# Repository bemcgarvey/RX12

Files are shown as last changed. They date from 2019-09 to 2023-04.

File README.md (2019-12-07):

# RX12  
## A 12 channel radio control receiver that uses one to three Spektrum compatible satellite receivers.

### Features:  
* Up to 12 channels
* One to three satellite receivers for full diversity
* Works with DSMX or DSM2 satellites
* 22ms or 11ms output rate  
* Optional PPM output (up to 8 channels) or S.Bus output (12 channels)
* Preset or hold failsafe modes
* PC client program with serial connection
* Simple data logging of multiple flights
* 32 bit microcontroller at 120MHz

Note: This is not a Spektrum DSMX or DSM2 product, nor is it a copy of a Spektrum DSM2 or DSMX product. The Spektrum, DSMX and DSM2 brand is a trademark of Horizon Hobby, Inc.

User manual is [here](https://github.com/bemcgarvey/RX12/blob/master/docs/RX12%20Manual.pdf)  
Gerber files and schematics can be found in PCB and Schematic folders.  
Firmware built with XC32 2.10 and MPLAB X.  Client code built with Qt 5.12  

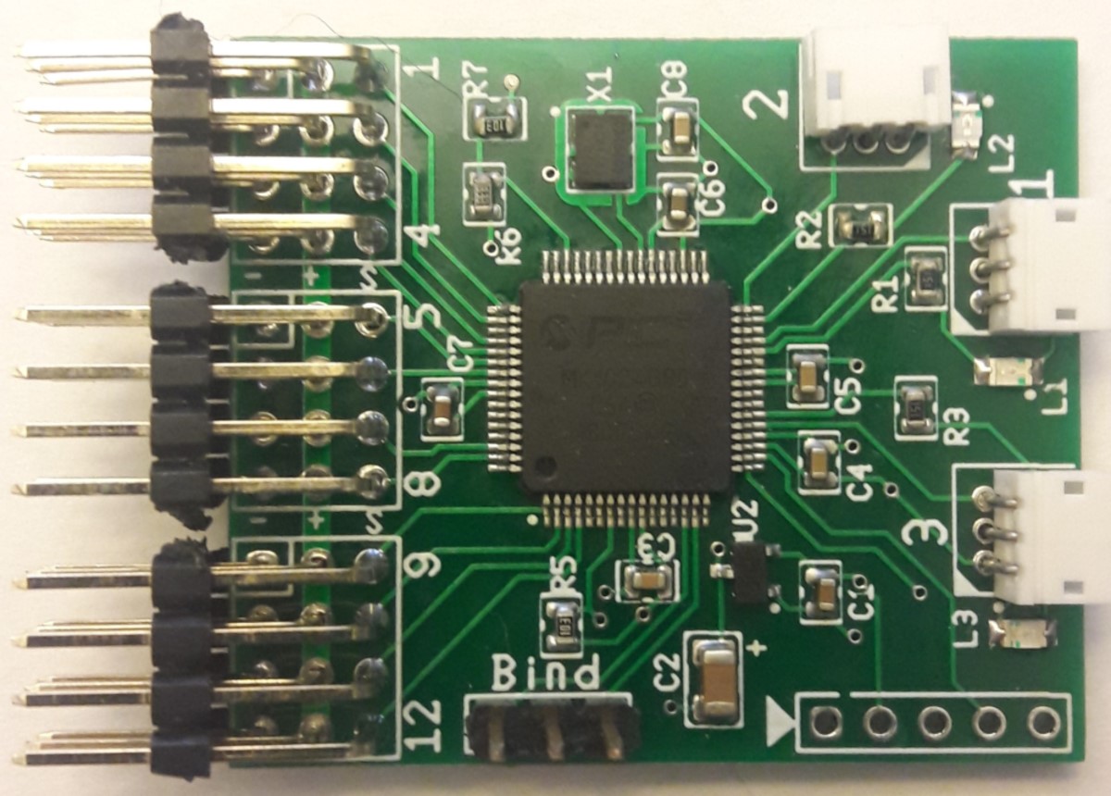
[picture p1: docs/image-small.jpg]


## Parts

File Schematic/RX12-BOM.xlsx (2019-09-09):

Quantity | Description | RefDes | Package | Digikey Part
3 | ZH-3 Side connectors | J4, J5, J6 | Ultiboard\ZH-3-Side | 455-1670-ND
3 | Headers, HDR3X4 | J2, J3, J8 | Ultiboard\HDR3X4
1 | VoltageRegulator, AP2210N-3.3 | U2 | Philips\SOT-23 | AP2210N-3.3TRG1DICT-ND (https://www.digikey.com/product-detail/en/diodes-incorporated/AP2210N-3.3TRG1/AP2210N-3.3TRG1DICT-ND/4505294)
1 | CAPACITOR, 2.2µF | C1 | Ultiboard\C0603
1 | CAPACITOR, 10µF | C2 | Ultiboard\C1206
1 | HEADERS_TEST, HDR1X5 | J1 | Generic\HDR1X5
1 | PIC32, PIC32MKxxxGPD/E064 | U1 | Microchip\TQFP-64(PT)
1 | Xtal, Osc 24 MHz | X1 | Osc-3225 | DSC6001CI2A-024.0000-ND (https://www.digikey.com/product-detail/en/microchip-technology/DSC6001CI2A-024.0000/DSC6001CI2A-024.0000-ND/7732678)
3 | LED_green | L1, L2, L3 | Ultiboard\0805LED
3 | RESISTOR, 150Ω | R1, R2, R3 | Ultiboard\R0603
6 | CAPACITOR, 0.1µF | C3, C4, C5, C6, C7,C8 | Ultiboard\C0603
2 | RESISTOR, 10kΩ | R5, R7 | Ultiboard\R0603
1 | RESISTOR, 33kΩ | R6 | Ultiboard\R0603
1 | HEADERS_TEST, HDR1X3 | J7 | Generic\HDR1X3

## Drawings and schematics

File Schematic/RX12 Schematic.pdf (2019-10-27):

0

1

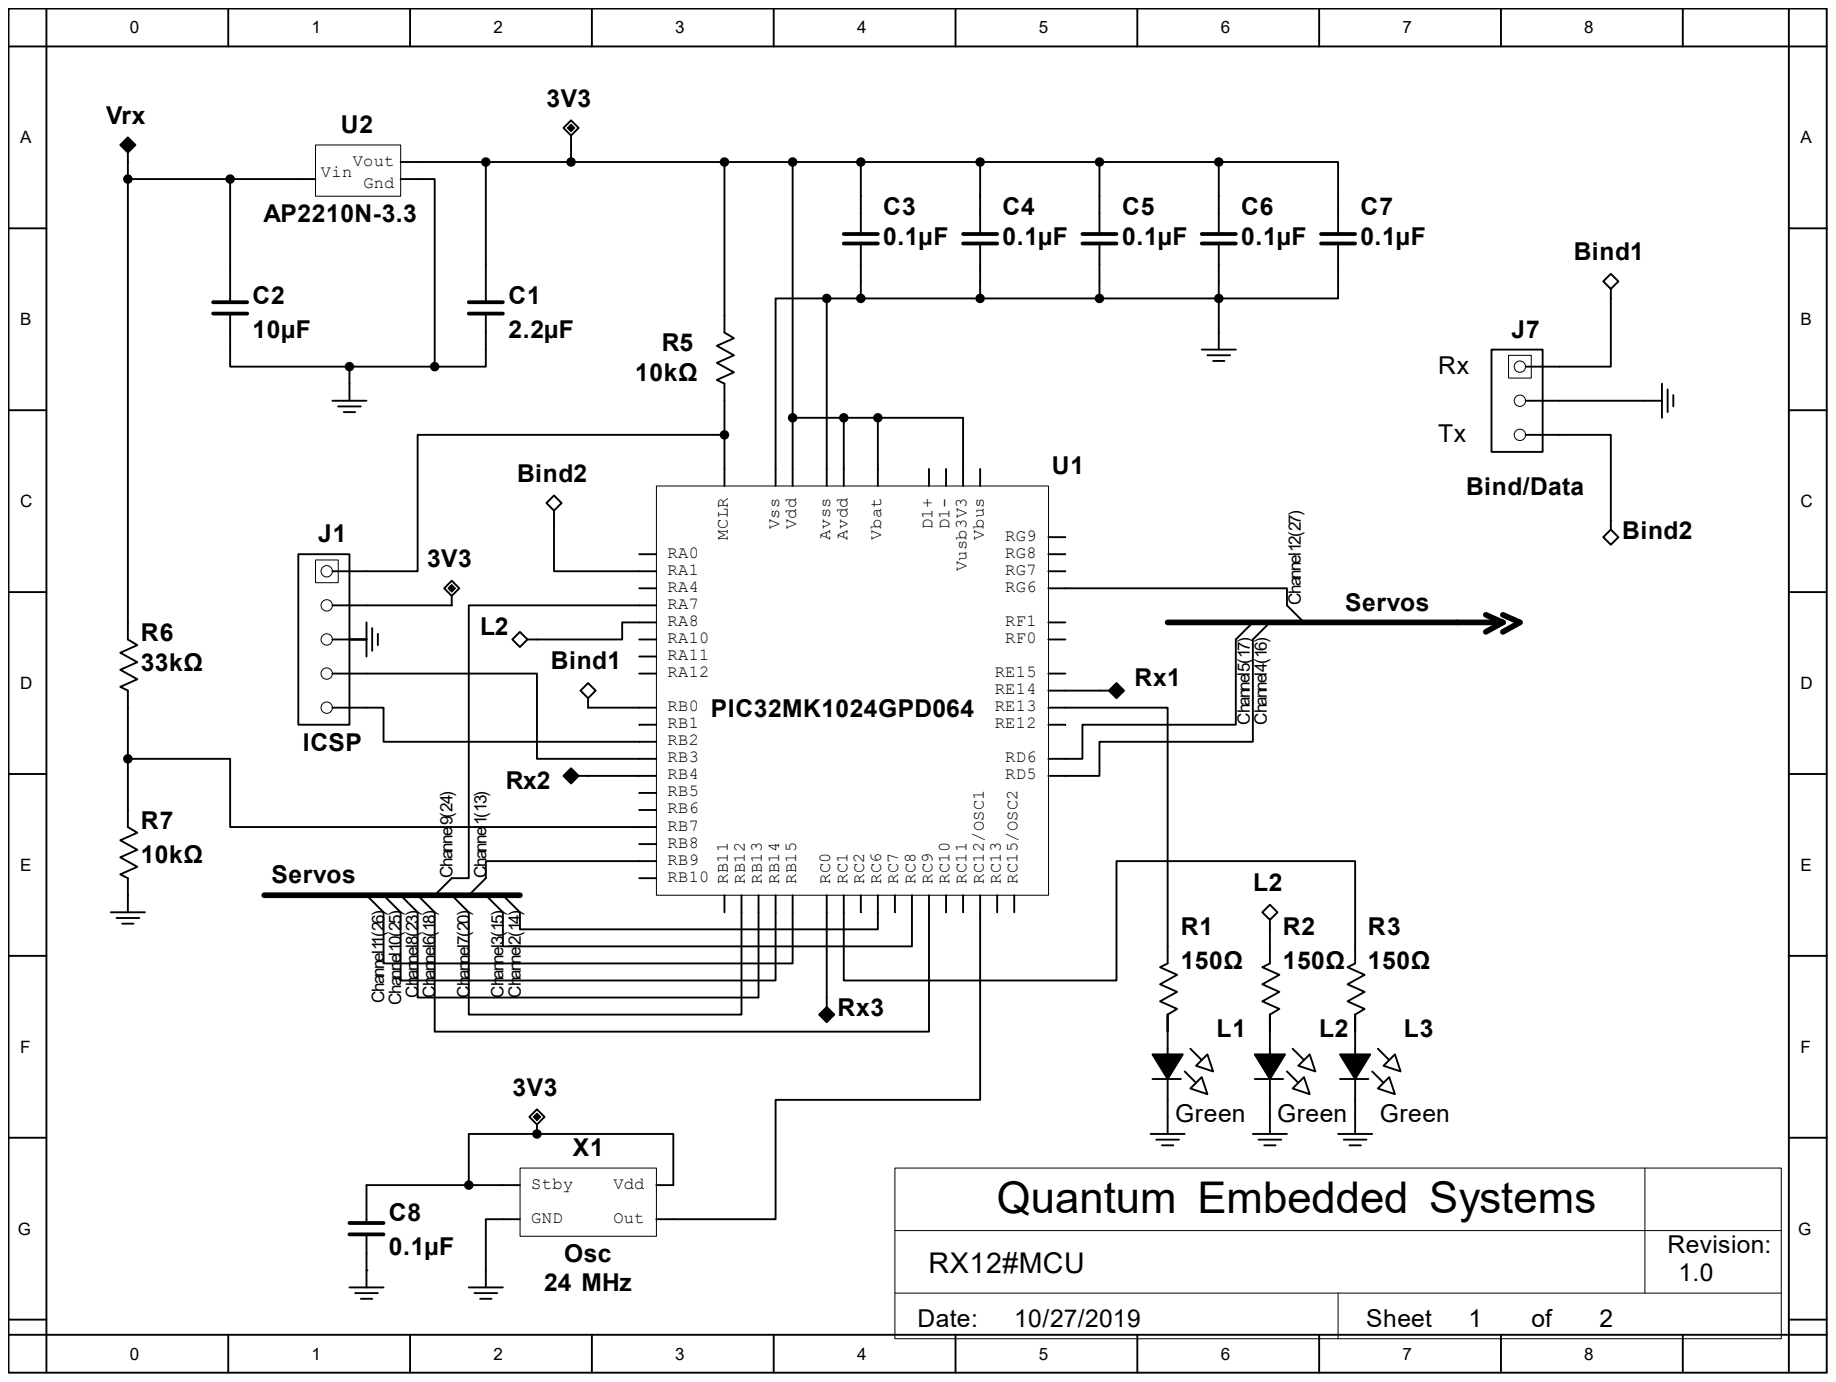
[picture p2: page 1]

0

1

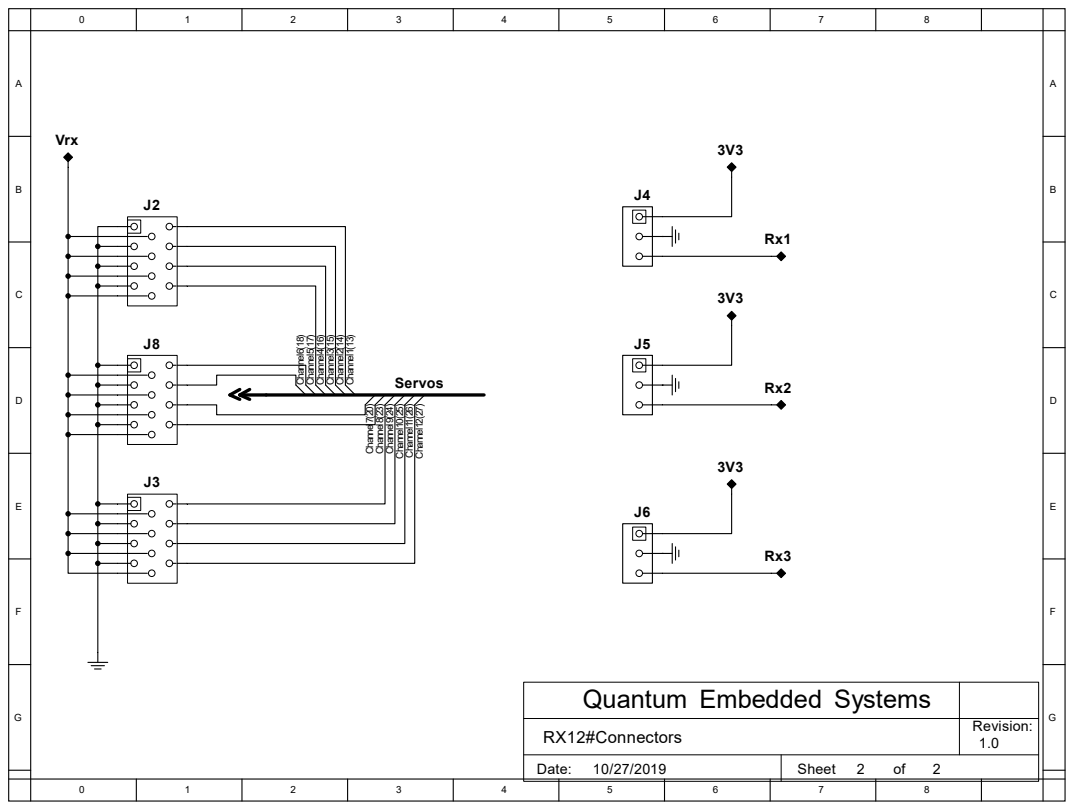
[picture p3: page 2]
Vrx; Channel4⁽ 16⁾ Channel3⁽ 15⁾ Channel2⁽ 14⁾ Channel1⁽ 13⁾; Servos; Channel6⁽ 18⁾ Channel5⁽ 17⁾; Channel7⁽ 20⁾ Channel8⁽ 23⁾ Channel9⁽ 24⁾ Channel10⁽ 25⁾ Channel11⁽ 26⁾ Channel12⁽ 27⁾; Date:; Sheet; Revision:; RX12#Connectors

Quantum Embedded Systems

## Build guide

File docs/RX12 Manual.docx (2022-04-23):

RX12

Manual

Version 1.5

April 2022

Firmware Version 1.8

Software Version 1.4

# Table of Contents

1. Overview
2. Connections and LED codes
3. Binding
4. Output formats and channel order
5. Client software
6. Data logging

# Overview

The RX12 receiver turns one or more DSMX/DSM2 satellite receivers into a full capability receiver with up to 12 channels. It supports the following features:

- Supports DSMX-11ms, DSMX-22ms, DSM2-2048 and DSM2-1024 transmitter modes. Note that you must use DSMX-22ms to receive 12 channels. The maximum channels in DSMX-11ms mode is 10. This is a Spektrum limitation and not an issue with the receiver.
- 12 channel PWM or S.Bus output with 22ms or 11ms servo frame rate or a single PPM output with up to 8 channels. The S.Bus outputs include all 18 S.Bus channels but only channels 1-10 are output on the PWM pins.
- Configurable failsafe - hold (no throttle signal) or user preset failsafe
- Can support up to three satellite receivers for full diversity.
- Limited data logging.
- Updatable firmware.

Note: This is not a Spektrum DSMX or DSM2 product, nor is it a copy of a Spektrum DSM2 or DSMX product. The Spektrum, DSMX and DSM2 brand is a trademark of Horizon Hobby, Inc.

# Connections and LED codes

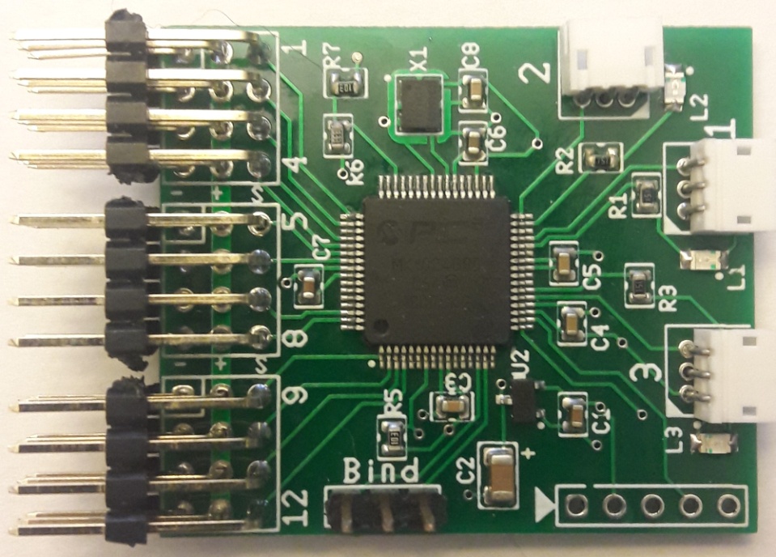
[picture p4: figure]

Tx Gnd Rx

Satellite Ports

L1, L2 and L3 are LED1, LED2 and LED3

ICSP Port

Bind/Serial Port

Servo outputs

Connection descriptions

Satellite ports: Connect one or more DSMX/DSM2 satellites to these ports. Any port may be used, they do not need to be connected in any order. You can connect satellites to any combination of ports. The only requirement is that all satellites must be of the same type, either all DSMX or all DSM2. Each port has an associated LED for status indication.

Bind/Serial port: Used to bind the receiver to the transmitter and for serial communication to a PC. See the Binding section of the manual for information on binding. See the Client Software section for information on serial communication.

ICSP port: Used to update the firmware. Not normally used.

Servo outputs: Connections to the servos. The channels are labeled on the board. Channels 1 – 4 are grouped together then 5 – 8 and 9 – 12. Channels 11 and 12 can also be used during the binding process. See the Binding section for details. Channel 12 is used for PPM output if enabled. Channels 11 and 12 are used for S.Bus outputs if enabled. The signal pin is the upper pin (or rightmost if oriented as in the picture above on top pin versions). The ground pin is the bottom (or leftmost) pin. The center pin is power.

Led codes

LED1 On solid = satellite connected and receiving data

Four flashes at startup = Logging enabled

LED2 On solid = satellite connected and receiving data

Two flashes at startup = Preset failsafe mode

LED3 On solid = satellite connected and receiving data or serial connection established

No flash at startup = PWM with 22ms servo frame

One flash at startup = PWM with 11ms servo frame

Two flashes at startup = PPM mode

Three flashes at startup = S.Bus mode with 22ms servo frame

Four flashes at startup = S.Bus mode with 11ms servo frame

10 flashes at startup = bind mode

# Binding

To bind the receiver to a transmitter follow the steps below.

1. Connect one or more satellite receivers to the satellite ports.
2. Place a bind plug on the bind connector.
3. If you are using DSM2 satellites place a bind plug on Channel 11.
4. If you want to enable 11ms output frame rate place a bind plug on Channel 12. This can also be enabled at a later time either with a bind process or with the PC software.
5. Connect the receiver to an ESC or battery. LED3 should blink rapidly 10 times and the satellites should blink to indicate bind mode.
6. Place the transmitter into bind mode and complete the bind. DO NOT unplug the bind plug at this time unless you want to enable preset failsafe (see next step.)
7. To enable the preset failsafe do the following. Go to step 8 for normal failsafe.
  a. Use the transmitter to set the servos in the desired positions.
  b. With the servos in the correct positions remove the bind plug.
  c. You can now power off the receiver.
8. For normal failsafe (no signal to throttle, all other channels hold) remove the power from the receiver BEFORE removing the bind plug. Don’t forget to remove the bind plug!

Note: Some servos may be detected as a bind plug. When binding it is best not to have a servo plugged into channels 11 or 12 as it may be detected as a bind plug. If you must have a servo plugged into these channels plug it in after LED3 stops flashing.

To enable/disable 11ms output frame rate after the receiver has been bound:

1. Plug a bind plug into the bind port.
2. Plug a bind plug into Channel 12 to enable 11 ms mode. Leave Channel 12 open to disable 11ms mode.
3. Power the receiver. LED3 will blink 10 times and the satellites will be in bind mode.
4. DO NOT rebind the transmitter. After the receiver quits blinking remove the power THEN remove the bind plugs. The next time the receiver is powered up it will blink LED3 to indicate it is in 11ms mode.

Note that 11ms output frame rate is independent from the transmitter frame rate. You may use 11ms output with DSMX-22ms mode or use 22ms output with DSMX-11ms mode. Any combination is allowed. However, you should only use the 11ms output with digital servos.

# Output formats and channel order

The receiver can output to the servos or a flight controller in the following formats:

- Standard PWM outputs on the 12 numbered servo output pins.
- PPM output of up to 8 channels on the Channel 12 pins. In PPM mode there is no output on the channel 1 – 11 pins.
- S.Bus output of up to 18 channels on Channel 11 and 12 pins. Channels 1 – 10 are also output on the PWM pins at 11ms or 22ms as selected during bind or by the client software.

To switch to PPM or S.Bus output you must use the client software to switch modes. See the next section for details on the client software.

Channel ordering

For PWM output the channels follow the standard Spektrum order:

2. Throttle
3. Aileron
4. Elevator
5. Rudder
6. Gear
7. Flaps
8. Aux1
9. Aux2
10. Aux3
11. Aux4
12. Aux5
13. Aux6

S.Bus and PPM outputs use the Futaba AETR ordering:

(Note: The order below is the channel order for the S.Bus outputs. The PWM pins will output with the order shown above for PWM outputs.)

(Note: PPM only supports channels 1-8)

1. Aileron
2. Elevator
3. Throttle
4. Rudder
5. Gear
6. Flaps
7. Aux1
8. Aux2
9. Aux3
10. Aux4
11. Aux5
12. Aux6

# Client Software

The receiver can be connected to a PC through the bind/serial port. The client software can be used to read or set some of the configuration settings. It can also be used to retrieve data logged during previous flights. To connect the receiver to a PC you will need a USB to Serial bridge that supports 3.3V levels.

To connect:

1. Make sure the USB to Serial adapter is set for 3.3V. A 5V adapter will damage or destroy the receiver.
2. Connect the ground of the adapter to the middle pin of the bind port.
3. Connect the TX of the adapter to the RX pin of the bind port (see picture in Connections section.)
4. Connect the RX of the adapter to the TX pin of the bind port.
5. Plug the USB to Serial adapter into your computer.
6. Connect an ESC or battery to the receiver. LED3 should light up and remain on.
7. Start the client software.
8. Select the Port menu then select the port that corresponds to your USB to Serial adapter. The status bar at the bottom of the window should show that you are connected.
9. Click the Read button to read the settings.
10. Make any changes you want and then click the Save button to save them to the receiver.
11. To download flight logs change to the Data tab. Select the number of logs to download (starting with the most recent) and click the Load button.
12. Clicking the Reset Log button will clear all current logs and restart the numbering at 1.

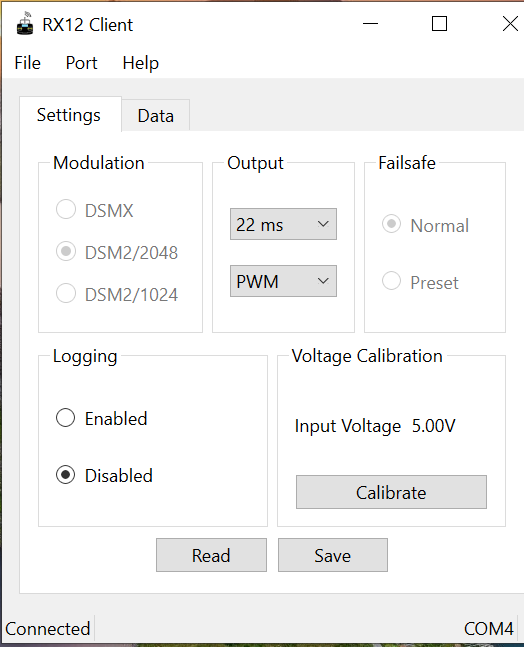
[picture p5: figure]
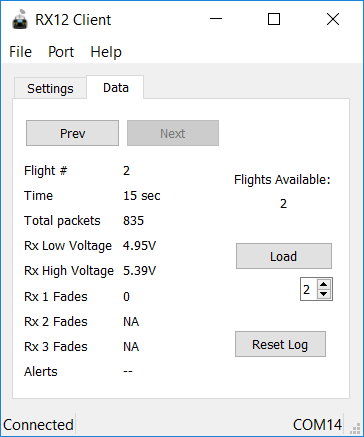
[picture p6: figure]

Voltage Calibration

The voltage input must be calibrated before it will give meaningful results. You can do a one point or two point calibration. A two point calibration is more accurate but requires two different voltages with at least 1.0V difference. A 2.0V or more difference is recommended. This will require a variable power supply that can be connected to the receiver

To perform a one point calibration:

1. With the receiver connected to the serial adapter and powered on, accurately measure the input voltage to the receiver.
2. Click the calibrate button.
3. Enter the measured input voltage in the dialog.
4. Click Next
5. Click Single Value to complete the calibration.

To perform a two point calibration

1. While connected to the serial adapter and powered on set the input voltage to the receiver to a known value between 4.0V and 12.0V.
2. Click the calibrate button.
3. Enter the input voltage in the dialog.
4. Click Next
5. Set the input voltage to a new value. It can be higher or lower than the first voltage but should be at least a one volt difference. It is best to use voltages that cover the expected operating range of the receiver.
6. Enter the new input voltage in the dialog.
7. Click Next to complete the calibration.

# Data Logging

If enabled the receiver will log the following data for each time it is powered on:

- Power on duration
- Total packets received by all satellites
- Input high and low voltage.
- Fades for each satellite.
- Any error conditions detected including activation of the failsafe feature.

Notes:

- Data is sampled continuously but is only saved to flash memory every second.
- In the event of a power failure or brownout the last second of data may be lost.
- Voltages are checked every millisecond.
- Fades are recorded with each satellite packet.
- It is not recommended to use data logging for every flight. Continuous use will eventually wear out the flash memory used to save the logs. This will not affect the operation of the receiver but will prevent any more logging. Just turn on logging when you want to see how the receiver is functioning in a new setup or with a different satellite configuration etc.

Alert Codes - The following codes may show up in the Alerts display:

- FS = Failsafe

The failsafe engaged at some time during the flight. This means none of the satellites had a signal at that time.

- WD = Watchdog

A watchdog reset occurred. This is bad. It means the code locked up at some point. Report this to the designer.

- CF = Clock Failure

The on board oscillator has failed and the backup internal oscillator had to take over. The receiver will still function but may not be fully reliable. This should almost never happen but if you see this error it is recommended to replace the receiver.

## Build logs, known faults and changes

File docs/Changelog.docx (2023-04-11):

# RX12 Changelog

# Firmware

Version 1.0 – First tested and flown version.

Version 1.01

- If receiver is powered on before transmitter the log will no longer show a Failsafe alert.

Version 1.2

- Added PPM output option on Ch. 12 pins.

Version 1.3

- Added sBus output option on Ch. 12 pins.
- Changed blink codes to make them easier to distinguish.

Version 1.4

- Changed PPM output order to AETR to maintain compatibility with PPM encoders.
- Fixed sBus bug – Throttle channel was incorrect.
- sBus failsafe bit was in wrong position.

Version 1.5

- PWM outputs 1-11 are now active even in sBus mode. Output 12 is used for sBus so channel 12 is not available in PWM format.

Version 1.6

- Outputs 11 and 12 are disabled whenever rx is powered up in bind mode. This prevents these outputs from becoming active with a bind plug attached and shorting the pin to ground. Power cycling will enable outputs.

Version 1.7

- If sBus mode is selected you can now select 11ms or 22ms for the servo frame rate. Previous versions only allowed 22ms when using sBus. Added blink code for sBus 11ms.

Version 1.8

- In sBus mode the pins for channels 11 and 12 are both sBus outputs. Channels 11 and 12 are not available in PWM format.

Version 1.9

- Enabled brown-out reset. Now it handles a brown-out like a watchdog reset and restarts quickly.
- S.Bus failsafe bit was in wrong position. Fixed.

Version 1.10

- Fixed preset failsafe bug. EEPROM address was incorrect.
- sBus baud rate was slightly off.

# Client

Version 1.00 – Initial version

Version 1.1 – Added PPM option

Version 1.2 – Added S.Bus option

Version 1.3 – Changed connection behavior. Now only reports “Connected” after successful read. Now Save button is only enabled after successful read.

Version 1.4 – UI changes to accommodate firmware version 1.7 Should still work with older versions.

Version 1.5 – Fixed Firmware Version display in About dialog

# Schematic and PCB

Version 1.0 – Initial production version

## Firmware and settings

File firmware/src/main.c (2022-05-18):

/////////////////////////////////////////////////////
// Project: RX12                                   //
// File: main.c                                    //
// Target: PIC32MKxxxxGPD/E064                     // 
// Compiler: XC32 (Tested with 2.10)               //
// Author: Brad McGarvey                           //
// License: GNU General Public License v3.0        //
// Description: program entry point and nmi handler//
/////////////////////////////////////////////////////
#include <xc.h>
#include <stddef.h>                     // Defines NULL
#include <stdbool.h>                    // Defines true
#include <stdlib.h>                     // Defines EXIT_FAILURE
#include "definitions.h"                // SYS function prototypes
#include "startup.h"
#include "satellite.h"
#include "led.h"
#include "timers.h"
#include "uart.h"
#include "datapacket.h"
#include "output.h"
#include "pins.h"
#include "failsafe.h"
#include "eeprom.h"
#include "failsafe.h"
#include "logging.h"
#include "serial.h"

static unsigned int lastSat1;
static unsigned int lastSat2;
static unsigned int lastSat3;

int main(void) {
    int result;

    startupMode = START_NORMAL;
    if (RCONbits.POR == 1) {
        //power on reset
        RCONbits.POR = 0;
        RCONbits.BOR = 0;
    } else if (RCONbits.WDTO == 1) {
        startupMode = START_WDTO;
        RCONbits.WDTO = 0;
    } else if (RCONbits.BOR == 1) {
        startupMode = START_WDTO; //Treat a brown-out like a WDT reset - start quickly
        RCONbits.BOR = 0;
    }
    SYS_Initialize(NULL);
    initPins();
    initEEPROM();
    if (startupMode != START_WDTO) {
        DetectStartupMode();
    }
    if (startupMode == START_BIND) {
        DetectConnectedSatellites();
        SendBindPulses(bindType);
        writeEEPROM(ADDRESS_FRAME_RATE, frameMode);
    } else {
        readEEPROM(ADDRESS_PRIMARY_SAT, &primarySatellite);
        if (primarySatellite > SAT3) {
            primarySatellite = SAT1;
        }
    }
    outputType = OUTPUT_TYPE_PWM;
    unsigned int savedOutputType = 0;
    result = readEEPROM(ADDRESS_OUTPUT_TYPE, &savedOutputType);
    if (result == EEPROM_SUCCESS) {
        if (savedOutputType == OUTPUT_TYPE_PWM || savedOutputType == OUTPUT_TYPE_PPM
                || savedOutputType == OUTPUT_TYPE_SBUS) {
            outputType = savedOutputType;
        } else {
            writeEEPROM(ADDRESS_OUTPUT_TYPE, outputType);
        }
    }
    setPPS();
    if (startupMode == START_SERIAL) {
        LED3On();
        initSerial();
        __builtin_set_isr_state(0);
        __builtin_enable_interrupts();
        while (true);
    }
    FrameMode savedFrameMode = 0;
    result = readEEPROM(ADDRESS_FRAME_RATE, &savedFrameMode);
    if (result == EEPROM_SUCCESS) {
        if (savedFrameMode == FRAME_22MS || savedFrameMode == FRAME_11MS) {
            frameMode = savedFrameMode;
        } else {
            writeEEPROM(ADDRESS_FRAME_RATE, frameMode);
        }
    }
    FailsafeType savedFailsafeType = HOLD_FAILSAFE;
    result = readEEPROM(ADDRESS_FAILSAFE_TYPE, &savedFailsafeType);
    if (result == EEPROM_SUCCESS) {
        if (savedFailsafeType == HOLD_FAILSAFE || savedFailsafeType == PRESET_FAILSAFE) {
            failsafeType = savedFailsafeType;
        } else {
            writeEEPROM(ADDRESS_FAILSAFE_TYPE, failsafeType);
        }
    }
    if (failsafeType == PRESET_FAILSAFE) {
        if (!loadFailsafePresets()) {
            failsafeType = HOLD_FAILSAFE;
        }
    }
    unsigned int blinks = 0;
    if (startupMode != START_WDTO) {
        if (outputType == OUTPUT_TYPE_PWM && frameMode == FRAME_11MS) {
            blinks = 1;
        } else if (outputType == OUTPUT_TYPE_PPM) {
            blinks = 2;
        } else if (outputType == OUTPUT_TYPE_SBUS) {
            blinks = 3;
            if (frameMode == FRAME_11MS) {
                blinks = 4;
            }
        }
    }
    if (startupMode == START_BIND) {
        blinks = 10;
    }
    for (unsigned int i = 0; i < blinks; ++i) {
        LED3On();
        delay_us(200000);
        LED3Off();
        delay_us(200000);
    }
    if (failsafeType == PRESET_FAILSAFE && startupMode != START_WDTO) {
        for (unsigned int i = 0; i < 2; ++i) {
            LED2On();
            delay_us(200000);
            LED2Off();
            delay_us(200000);
        }
    }
    __builtin_set_isr_state(0);
    __builtin_enable_interrupts();
    startSystemTickTimer();
    initOutputs();
    if (frameMode == FRAME_22MS || outputType == OUTPUT_TYPE_PPM) {
        startOCTimer(PERIOD_22MS);
    } else {
        startOCTimer(PERIOD_11MS);
    }
    initUARTs();
    if (startupMode == START_BIND) {
        while (startupMode == START_BIND) {
            if (packetQueueHead != packetQueueTail) {
                systemType = checkPacketType(primarySatellite);
            }
            if (systemType != SYSTEM_TYPE_NONE) {
                startupMode = START_NORMAL;
            }
        }
        writeEEPROM(ADDRESS_DSM_TYPE, systemType);
    } else {
        systemType = SYSTEM_TYPE_DSMX_11;
        DSMSystemType savedSystemType;
        if (readEEPROM(ADDRESS_DSM_TYPE, &savedSystemType) == EEPROM_SUCCESS) {
            if (savedSystemType == SYSTEM_TYPE_DSM2_1024 ||
                    savedSystemType == SYSTEM_TYPE_DSM2_2048 ||
                    savedSystemType == SYSTEM_TYPE_DSMX_11 ||
                    savedSystemType == SYSTEM_TYPE_DSMX_22) {
                systemType = savedSystemType;
            }
        }
        checkLoggingActive();
        if (logging) {
            if (startupMode != START_WDTO) {
                for (unsigned int i = 0; i < 4; ++i) {
                    LED1On();
                    delay_us(200000);
                    LED1Off();
                    delay_us(200000);
                }
            }
            startLogging();
        }
    }
    WDTCONbits.WDTCLRKEY = 0x5743;
    RCONbits.WDTO = 0;
    WDTCONbits.ON = 1; //Turn on WDT
    while (true) {
        if (packetQueueHead != packetQueueTail) {
            processCurrentPacket();
        }
        if (!outputsActivated && packetsReceived > 10) {
            enableActiveOutputs();
            outputsActivated = true;
        }
        if (systemTickCount > 100) {
            lastSat1 = systemTickCount - lastPacket[SAT1];
            lastSat2 = systemTickCount - lastPacket[SAT2];
            lastSat3 = systemTickCount - lastPacket[SAT3];
            if (lastSat1 < 100) {
                LED1On();
            } else {
                LED1Off();
            }
            if (lastSat2 < 100) {
                LED2On();
            } else {
                LED2Off();
            }
            if (lastSat3 < 100) {
                LED3On();
            } else {
                LED3Off();
            }
            if (!failsafeEngaged && lastSat1 > 100 && lastSat2 > 100 && lastSat3 > 100) {
                if (failsafeType == PRESET_FAILSAFE) {
                    for (int i = 0; i < MAX_CHANNEL; ++i) {
                        outputPulses[i] = presetOutputPulses[i];
                    }
                } else {
                    disableThrottle();
                }
                servos[THROTTLE] = 0xffff; //Mark throttle as inactive
                if (outputsActivated) {
                    currentFlightLog.statusFlags |= STATUS_FAILSAFE;
                }
                failsafeEngaged = true;
            }
            if (failsafeEngaged && servos[THROTTLE] != 0xffff) {
                if (failsafeType == HOLD_FAILSAFE) {
                    enableThrottle();
                }
                failsafeEngaged = false;
            }
        }
        WDTCONbits.WDTCLRKEY = 0x5743;
    }
    return ( EXIT_FAILURE);
}

void _nmi_handler(void) {
    int wdtFlag;
    wdtFlag = WDTCONbits.ON;
    WDTCONbits.ON = 0;
    if (RNMICONbits.CF == 1) {
        SYSKEY = 0x00000000;
        SYSKEY = 0xAA996655;
        SYSKEY = 0x556699AA;
        SPLLCONbits.PLLIDIV = 0b000; //according to datasheet PLLIDIV is ignored when FRC is selected
        SPLLCONbits.PLLICLK = 1;
        OSCCONbits.FRCDIV = 0;
        OSCCONbits.NOSC = 0b001;
        OSCCONbits.OSWEN = 1;
        OSCCONbits.CF = 0;
        RNMICONbits.CF = 0;
        SYSKEY = 0x33333333;
        while (OSCCONbits.OSWEN == 1);
        currentFlightLog.statusFlags |= STATUS_CF;
    }
    //Clear BEV flag
    _CP0_BIC_STATUS(_CP0_STATUS_BEV_MASK);
    WDTCONbits.WDTCLRKEY = 0x5743;
    WDTCONbits.ON = wdtFlag;
    __asm__("ERET");
}

/*******************************************************************************
 End of File
 */

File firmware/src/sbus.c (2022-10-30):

/////////////////////////////////////////////////////
// Project: RX12                                   //
// File: sbus.c                                    //
// Target: PIC32MKxxxxGPD/E064                     // 
// Compiler: XC32 (Tested with 2.10)               //
// Author: Brad McGarvey                           //
// License: GNU General Public License v3.0        //
// Description: S.Bus output code                  //
/////////////////////////////////////////////////////

#include <xc.h>
#include "sbus.h"
#include "output.h"
#include <sys/attribs.h>
#include <stdint.h>
#include "failsafe.h"
#include "timers.h"

#define SBUS_HEADER 0x0f;
#define SBUS_FOOTER 0x00;

volatile SBusPacket __attribute__((aligned(4))) sbusPacket;

static volatile int bytesRemaining = 0;
static volatile int currentPos = 0;

void initSBus(void) {
    //Setup UART1
    //100000 baud, 8E2, inverted polarity
    U1MODEbits.CLKSEL = 0b01; //SYSCLOCK
    U1BRG = 74; //100000 baud
    U1MODEbits.BRGH = 0;
    U1MODEbits.PDSEL = 0b01; //8E
    U1MODEbits.STSEL = 1; //2 stop bits
    U1STAbits.UTXINV = 1; //invert
    U1STAbits.UTXISEL = 0b10; //interrupt when tx buffer empty
    IPC10bits.U1TXIP = 6;
    IPC10bits.U1TXIS = 0;
    //initialize packet;
    for (int i = 0; i < 25; ++i) {
        sbusPacket.bytes[i] = 0;
    }
    sbusPacket.header = SBUS_HEADER;
    sbusPacket.footer = SBUS_FOOTER;
}

void startSBus(void) {
    for (int i = 0; i < MAX_CHANNEL; ++i) {
        if (servos[i] == 0xffff) {
            servos[i] = 1024;  //set inactive channels to midpoint value;
        }
    }
    //Timer 4/5 in 32bit mode 
    T4CONbits.ON = 0;
    Nop();
    T4CONbits.T32 = 1; //32 bit
    T4CONbits.TCKPS = 0; //1:1
    TMR4 = 0;
    PR4 = MS_COUNT * PERIOD_SBUS;
    IPC4bits.T4IP = 6;
    IPC4bits.T4IS = 0;
    IFS0bits.T4IF = 0; 
    IFS1bits.U1TXIF = 0;
    U1MODEbits.ON = 1;
    IEC0bits.T4IE = 1; //enable frame timer interrupt
    T4CONbits.ON = 1;
}

void transmitSBusPacket(void) {
    //build packet - Use Futaba AETR order
    uint16_t throttle;
    if (servos[0] == 0xffff) {
        throttle = 0;
    } else {
        throttle = servos[0];
    }
    sbusPacket.channels[0] = servos[1];
    sbusPacket.channels[1] = (servos[1] >> 8) | (servos[2] << 3);
    sbusPacket.channels[2] = (servos[2] >> 5) | (throttle << 6);
    sbusPacket.channels[3] = (throttle >> 2);
    sbusPacket.channels[4] = (throttle >> 10) | (servos[3] << 1);
    sbusPacket.channels[5] = (servos[3] >> 7) | (servos[4] << 4);
    sbusPacket.channels[6] = (servos[4] >> 4) | (servos[5] << 7);
    sbusPacket.channels[7] = (servos[5] >> 1);
    sbusPacket.channels[8] = (servos[5] >> 9) | (servos[6] << 2);
    sbusPacket.channels[9] = (servos[6] >> 6) | (servos[7] << 5);
    sbusPacket.channels[10] = (servos[7] >> 3);
    sbusPacket.channels[11] = servos[8];
    sbusPacket.channels[12] = (servos[8] >> 8) | (servos[9] << 3);
    sbusPacket.channels[13] = (servos[9] >> 5) | (servos[10] << 6);
    sbusPacket.channels[14] = (servos[10] >> 2);
    sbusPacket.channels[15] = (servos[10] >> 10) | (servos[11] << 1);
    sbusPacket.channels[16] = (servos[11] >> 7);
    sbusPacket.flags = 0;
    if (failsafeEngaged) {
        sbusPacket.flags = 0x08;
    }
    //load first 8 bytes
    for (int i = 0; i < 8; ++i) {
        U1TXREG = sbusPacket.bytes[i];
    }
    U1STAbits.UTXEN = 1;
    IFS1bits.U1TXIF = 0;
    IEC1bits.U1TXIE = 1;
    currentPos = 8;
    bytesRemaining = 17;
}

void __ISR(_UART1_TX_VECTOR, IPL6SOFT) Uart1TxIsr(void) {
    if (bytesRemaining > 8) {
        for (int i = 0; i < 8; ++i) {
            U1TXREG = sbusPacket.bytes[currentPos];
            ++currentPos;
        }
        bytesRemaining -= 8;
    } else {
        IEC1bits.U1TXIE = 0;
        U1TXREG = sbusPacket.bytes[24];
    }
    IFS1bits.U1TXIF = 0;
}

void __ISR(_TIMER_4_VECTOR, IPL6SOFT) Timer4Isr(void) {
    transmitSBusPacket();
    IFS0bits.T4IF = 0;
}

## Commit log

2019-06-14 Added schematic
2019-06-16 Schematic draft
2019-06-16 Revised schematic, added package info.
2019-06-16 Fixed broken ground connection
2019-06-16 Initial PCB layout
2019-06-17 Changed pin assignments
    To improve PCB layout
2019-06-17 Initial PCB design.
    All parts and connections placed. Not yet optimized. Silkscreen still needs work.
2019-06-18 Cleaned up silkscreen and added labels
2019-06-18 Cleaned up 3V3 trace
2019-06-18 Minor trace adjustments
2019-06-18 Changed servo connectors to 4 pin sets
2019-06-18 Generated gerber files
    [RX12.GBL, RX12.GBO, RX12.GBS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]
2019-06-18 Cleaned up schematic, added BOM.
    [RX12-BOM.xlsx]
2019-06-19 Changed to 24 MHz oscillator
    EC mode should be bettter based on errata.
    [RX12-BOM.xlsx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]
2019-06-20 Added guard around oscillator
    Ready to manufacture
    [RX12.GBL, RX12.GBS, RX12.GTL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]
2019-07-18 Updated BOM
    This is final version of schematic and PCB
    [RX12-BOM.xlsx]
2019-07-18 Satellite detection working. LED functions added.
2019-07-19 Timers started.
    Removed evic code. Fixed ANSEL in starup detect.
    [main.c]
2019-07-20 Removed Harmony clock code and set PB6 correctly
    Clock init moved to initialization.c
    [main.c, uart.c]
2019-07-20 Initial UART code working. Shadow register usage fixed
    [main.c]
2019-07-20 UART code working.
    Tested with 3 remotes. No errors found at this time.
    [datapacket.c, main.c, uart.c]
2019-07-21 Eliminated Harmony pps code. Improved pin init code.
2019-07-22 Outputs working. Hold failsafe implemented.
    Tested with 12 channels in DSMX/22 mode.
    [datapacket.c, main.c, output.c]
2019-07-22 Added 11ms/22ms frame rate binding
    [main.c]
2019-07-23 Watchdog timer implemented. LED blinks left in to indicate WDTO. Need to be removed before final version.
2019-07-23 Moved pulse calculation from timer ISR to processPacket()
2019-07-25 Changed LED resistors to 150 ohm to reduce current
    [RX12-BOM.xlsx]
2019-07-25 Changed shadow registers to UART ISRs instead of OCTimer
2019-07-27 Fail safe clock monitor implemented
    [main.c]
2019-07-27 Initial code for preset failsafe. Changes made to allow for different modes. Presets not yet saved.
    [main.c, output.c]
2019-07-27 Only check frame and dsm2 bind pins when in bind mode.
2019-07-30 First attempt at ADC code
2019-07-30 Fixed UART3 interrupt priorities
    [uart.c]
2019-08-03 Added voltage sensing for serial connection
2019-08-06 Fixes to serial. Beginning to work.
    [adc.c, serial.c]
2019-08-06 Save settings working except for calibration
2019-08-07 Voltage calibration working
2019-08-07 Changed interrupt priorities
2019-08-08 EEPROM interrupt write added
2019-08-08 Added Reset Log button
2019-08-09 Added single value calibration
2019-08-09 Logging working except for voltage
2019-08-09 Logging is working.
    Need to clean up the display and calculate real voltages
2019-08-10 Changed DSM2 bind pin to Channel 11 (vertical)
2019-08-10 Changed led functions to macros. Eliminated led.c
2019-08-13 Added pdf version of schematic
2019-08-14 Improved adc filtering
2019-08-14 Fixed throttle reference to use enum value
    [main.c]
2019-08-15 Minor fixes. WDTO blinks removed. Ready to fly.
    [main.c]
2019-08-17 Removed unused variables from UART code
2019-08-17 Fixed bug where spurious failsafe was being detected.
    [main.c]
2019-08-18 Separated last byte time from last packet time. Improved failsafe detection. Built with XC8 2.20
    [datapacket.c, main.c, uart.c]
2019-09-09 Updated schematic and BOM to AP2210N regulator.
    Also DSC6001 oscillator
    [RX12-BOM.xlsx]
2019-09-09 Fixed incorrect Failsafe alert
    When rx is powered on before tx it will no longer log an FS alert.
    [main.c]
2019-10-27 Update RX12 Schematic.pdf
2019-12-03 Initial PPM code stubs.
    PWM mode still works.
2019-12-04 Fixed missing breaks in command switch statement.
    [serial.c]
2019-12-06 Moved SAT1 to Uart5
2020-12-16 Fixed SBus bug
    Throttle channel was wrong and failsafe bit was in wrong position.
    [sbus.c]
2021-02-24 PWM outputs are now active in SBus mode
    Firmware Version 1.5
2021-08-23 Bind outputs are disabled when started in bind mode
    Solved a problem where an output could become active with a bind plug installed which would short the output. V1.6
    [pins.c, sbus.c]
2022-03-26 Added 11ms servo output for S.Bus mode
    Firmware version 1.7
    Client version 1.4
2022-04-23 Fixed voltage logging
    This has been broken since the logging timer was changed to TMR9.
    [adc.c]
2022-05-18 Enabled brown-out reset. Firmware V1.9
    [main.c, output.c]
2022-05-25 Fixed S.Bus flag bit position
    Only affected failsafe bit. All other outputs were correct.
    [sbus.c]
2022-10-30 Fixed sBus baud rate
    [sbus.c]
